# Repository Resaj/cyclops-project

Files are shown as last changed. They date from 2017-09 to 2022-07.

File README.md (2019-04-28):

# Cyclops-project

Robot siguelíneas Open Source, diseñado para introducir a nuevos constructores en la robótica de competición. Se compone de dos PCBs: la del chasis autosoportado con la electrónica principal; y la de sensores, que es intercambiable para poder adaptarlo a diferentes pruebas de seguimiento de línea. Incorpora extras de sensores de distancia, cámara y bluetooth, para poder participar en otras pruebas como carreras y laberinto, además de experimentar nuevos métodos de seguimiento de línea o degradado.

El chasis del robot incorpora:
- Arduino nano
- Batería Lipo 2S
- Pulsadores de selección de menú
- Leds indicadores
- Driver de motores TB6612FNG
- Micromotores 10:1 HP 6V con reductora metálica y encoders en cuadratura
- Ruedas de 32mm de diámetro
- Sensor frontal de distancia de 80cm para detección de oponentes (necesario para carreras)
- Sensores laterales de distancia de 35cm para detección de oponentes (necesario para carreras)
- Cámara de 1x128 píxeles para seguimiento de línea y detección de oponentes
- Expansor I2C para poder soportar todos los periféricos incorporados

La PCB de sensores es intercambiable e incorpora:
- Sensores CNY70 para seguimiento de línea (6 para velocista; 8 para rastreador)
- Multiplexor para los sensores de línea

<p align="center">
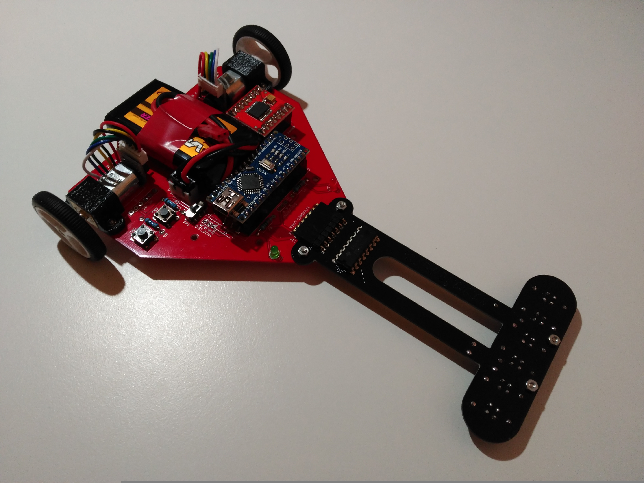
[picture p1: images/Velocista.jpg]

</p>

<p align="center">
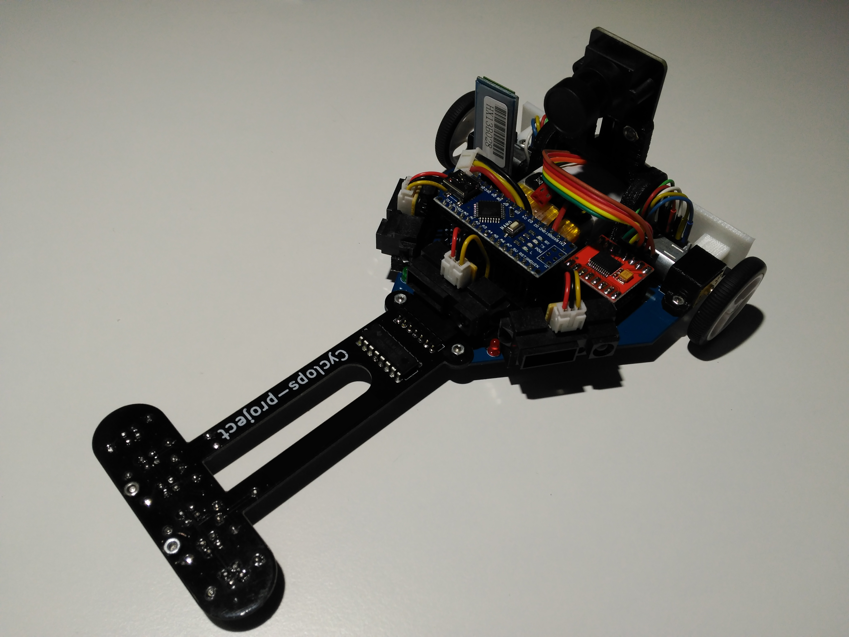
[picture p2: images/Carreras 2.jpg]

</p>

<p align="center">
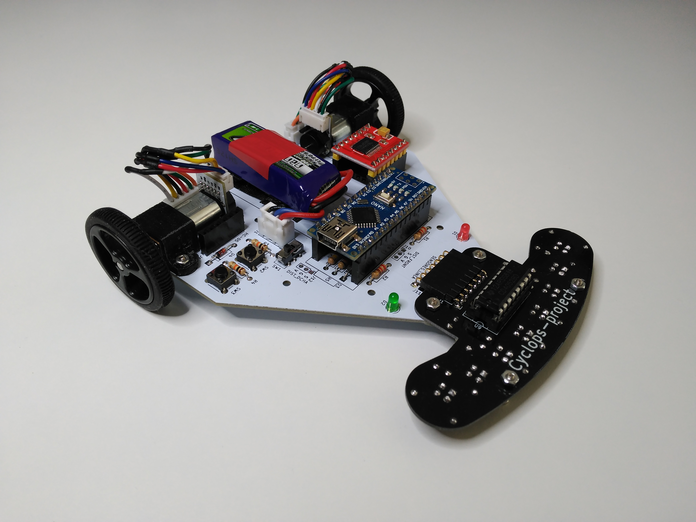
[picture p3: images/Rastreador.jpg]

</p>

## Manuales y guías del proyecto

Disponibles en la carpeta [manuals](https://github.com/Resaj/cyclops-project/tree/master/manuals):
- [Tutorial 1](https://github.com/Resaj/cyclops-project/blob/master/manuals/Tutorial%201%20-%20Bater%C3%ADas%20Lipo.pdf) - Baterías Lipo
- [Tutorial 2](https://github.com/Resaj/cyclops-project/blob/master/manuals/Tutorial%202%20-%20Impresi%C3%B3n%20de%20las%20piezas%20del%20robot.pdf) - Impresión de las piezas del robot
- [Tutorial 3](https://github.com/Resaj/cyclops-project/blob/master/manuals/Tutorial%203%20-%20Montaje%20del%20robot.pdf) - Montaje del robot
- [Tutorial 4](https://github.com/Resaj/cyclops-project/blob/master/manuals/Tutorial%204%20-%20Configuraci%C3%B3n%20del%20bluetooth%20HC-05.pdf) - Configuración del Bluetooth HC-05
- [Tutorial 5](https://github.com/Resaj/cyclops-project/blob/master/manuals/Tutorial%205%20-%20Primeras%20pruebas.pdf) - Primeras pruebas

A medida que el proyecto vaya avanzando se añadirán más tutoriales para completar la información y facilitar el montaje y la programación del robot.

## Retos planteados para el usuario

Cyclops es un proyecto base para cualquier persona que quiera adentrarse en el mundo de la robótica a través de las competiciones. Por un lado se proporciona una base para el aprendizaje y para facilitar la participación; por otro, se plantean una serie de retos e ideas que servirán a los usuarios para afrontar el desarrollo de un proyecto de robótica y profundizar experimentando con las mejoras:

* General:
  * Mejoras de comunicación por bluetooth con logs de telemetría
*  Rastreador:
  * [Reconocimiento de marcas de giro y selección del camino correcto en las bifurcaciones](https://www.youtube.com/watch?v=3Fi3WpjZuA0)
* Velocistas:
  * Reconocimiento de la [pista](https://github.com/Resaj/basic-circuit-maker) con encoders para acelerar en las rectas y frenar antes de las curvas
  * Adaptación del PID de seguimiento de línea para competir sobre [pistas de degradado](https://github.com/Resaj/circuit-maker)
* Carreras:
  * Detección de oponentes con los sensores de distancia para cambiar de carril y efectuar adelantamientos
  * Implementación de un PID para seguir a un oponente en carreras cuando no se pueda cambiar de carril para adelantar
  * Reconocimiento y seguimiento de líneas y degradados con cámara
* Laberinto:
  * Adaptación del algoritmo de laberinto para seguir la pared derecha en vez de la izquierda
  * Guiarse con los dos sensores laterales y con los encoders para ir siempre centrado en las casillas del laberinto
  * Memorizar las casillas del laberinto en el primer intento para que el robot sea capaz de resolverlo al segundo intento tomando el camino más corto

## Preguntas frecuentes

Puedes encontrar un listado de las preguntas frecuentes con sus respectivas respuestas en la [wiki del proyecto](https://github.com/Resaj/cyclops-project/wiki/FAQ).

## Autor

[Rubén Espino San José](https://github.com/Resaj)

## Agradecimientos y aportaciones

- A Alex @TCRobotics de BricoLabs, por su [tutorial para adaptar el driver CH340G de la Arduino Nano para MAC OS](https://bricolabs.cc/wiki/guias/mac_os_y_ch340)
- A [José Luis Villarejo](https://github.com/movilujo), por los [diseños de las PCBs de Cyclops en FreeCAD](https://github.com/Resaj/cyclops-project/tree/master/hw/FreeCAD/PCBs)
- A [Juan Alberto Babío](https://github.com/jbabio), por la adaptación del [soporte regulable para la cámara](https://github.com/Resaj/cyclops-project/blob/master/hw/FreeCAD/Soporte_inclinable_camara_Aliexpress.stl)
- A Óscar de BricoGeek, por sus streaming ([1](https://www.youtube.com/watch?v=NNreAwnH6MY) y [2](https://www.youtube.com/watch?v=S61M1Ss7pH4)) del montaje de Cyclops-Project
- A [Álex](https://github.com/robotaleh) y [Manuel](https://github.com/20leunam), de [OPRobots](https://github.com/OPRobots), por su [App para calibrar y controlar el robot mediante el bluetooth del móvil](https://github.com/Resaj/cyclops-project/tree/master/fw/PID_seguimiento_linea/PID_seguimiento_linea_PIDfromBT)
- A [Javier Martín](https://github.com/jamarju), por su [adaptación del bootloader de la Arduino para la carga de programas por bluetooth](https://github.com/jamarju/hexloader-avr)

## Licencia

<p align="center">



</p>

Todos estos productos están liberados mediante [Creative Commons Attribution-ShareAlike 4.0 International License](http://creativecommons.org/licenses/by-sa/4.0/).

_All these products are released under [Creative Commons Attribution-ShareAlike 4.0 International License](http://creativecommons.org/licenses/by-sa/4.0/)._

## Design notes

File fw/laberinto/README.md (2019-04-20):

# Programa de laberinto

Este programa sirve para testear el funcionamiento de un algoritmo PID básico para entrar y salir de un laberinto. Se trata de seguir una de las dos paredes. Por defecto está programado para que siga la pared izquierda.

Para que todo funcione correctamente debes haber seguido las indicaciones del [tutorial de primeras pruebas](https://github.com/Resaj/cyclops-project/blob/master/manuals/Tutorial%205%20-%20Primeras%20pruebas.pdf), donde aparecen las configuraciones necesarias para las diferentes partes del robot.

El led verde parpadeando indica que se encuentra en el estado "PARADO", preparado para correr. Para ponerlo en marcha hay que pulsar el botón izquierdo; para pararlo, el derecho.

El led rojo indica que la batería está baja.

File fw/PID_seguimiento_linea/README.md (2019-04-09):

# Programa PID_seguimiento_linea

Este programa sirve para testear el funcionamiento de un algoritmo PID básico para el seguimiento de líneas con el robot.

Para que todo funcione correctamente debes haber seguido las indicaciones del [tutorial de primeras pruebas](https://github.com/Resaj/cyclops-project/blob/master/manuals/Tutorial%205%20-%20Primeras%20pruebas.pdf), donde aparecen las configuraciones necesarias para las diferentes partes del robot.

Por defecto, el programa sigue la línea con los sensores de optorreflectancia, pero puede seguirla con la cámara si se descomenta la siguiente línea al comienzo del programa:

``` #define SEGUIMIENTO_CON_CAMARA ```

Para controlarlo se emplea la siguiente máquina de estados:

<p align="center">
<img src="maquina_de_estados.png" width="500" align = "center">
</p>

y los siguientes caracteres, que se envían como comandos a través de bluetooth o USB:
- '0' -> Parar (muy útil para parada de emergencia cuando se escapa el robot)
- '-' -> Bajar velocidad
- '+' -> Subir velocidad
- '1' -> Bajar Kp
- '7' -> Subir Kp
- '2' -> Bajar Ki
- '8' -> Subir Ki
- '3' -> Bajar Kd
- '9' -> Subir Kd

El led rojo indica que la batería está baja.

El led verde puede indicar lo siguiente:
- Si es fijo, se encuentra en el estado "INICIALIZADO".
- Si se enciende y se queda fijo mientras se encuentra en el estado "CALIBRANDO_SENSORES", quiere decir que los umbrales son aceptables y hay margen para una lectura correcta de la línea.
- Si parpadea, se encuentra en el estado "PARADO", preparado para correr.

Hay que tener en cuenta que, en el estado "CALIBRANDO_SENSORES", hay que mover el robot sobre la línea para que los sensores tomen los valores mínimos y máximos para poder calcular un umbral adecuado entre blanco y negro. Pulsar entonces el pulsador derecho para pasar al estado "PARADO". Es posible que al calibrar la cámara en este punto no se encienda el led verde porque los umbrales de blanco y negro son muy próximos entre ellos. El potenciómetro trasero de la cámara ajusta la ganancia de salida, modificando los valores de blanco y negro, pero aún así es difícil conseguir un buen resultado.

# Programa PID_seguimiento_linea_PIDfromBT

Una variante de PID_seguimiento_linea es el programa que puede encontrarse en la carpeta "PID_seguimiento_linea_PIDfromBT", adaptado por OPRobots para controlar el robot mediante su App para móvil, [PIDfromBT](https://github.com/robotaleh/PIDfromBT). La funcionalidad es la misma, pero el control puede realizarse desde el móvil.

Antes de cargarlo hay que instalar previamente su librería [PIDfromBTlib](https://github.com/robotaleh/PIDfromBTlib).

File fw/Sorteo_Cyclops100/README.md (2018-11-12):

# PROGRAMA PARA SORTEAR EL KIT 100 DE CYCLOPS-PROJECT EN LA OSHWDEM 2018

Este programa sirve para realizar un sorteo mediante la generación de un número aleatorio en el rango de números especificados. Para ello basta con fijar el número de participantes en el sorteo, cargar el programa en la Arduino de un Cyclops y abrir Monitor Serial, Putty o cualquier otro terminal que pueda comunicarse con el puerto serie de la Arduino. También se puede especificar el nombre de cada participante. Tras activar el pulsador aparecerá el número resultante en la pantalla.

El número obtenido es el resto de la división del número de milisegundos transcurridos desde el encendido de la Arduino (utilizando la función 'millis') entre el número de participantes.
Al utilizar la función 'millis' es imposible determinar de antemano cuál será el resultado del sorteo.
Por ejemplo:
- Hay 15 participantes
- El pulsador se ha activado en el milisegundo 5621
- El resto de 5621/15 es 11
- El afortunado es el participante con el número 11

Ya que el número 0 no se suele asignar a ningún participante en el sorteo, si saliese el 0 como el resto de la división mencionada anteriormente, el afortunado sería el participante con el número correspondiente al del número de participantes.
Por ejemplo:
- Hay 15 participantes
- El pulsador se ha activado en el milisegundo 9345
- El resto de 9345/15 es 0
- El afortunado es el participante número 15
Por eso en el código aparece el índice 0 asignado al participante con el número más alto.

-----------------------------------------------------

Finalmente, los ganadores del kit #100 de Cyclops-Project en la OSHWDem 2018 fueron los constructores de Pinturillo. ¡¡Enhorabuena!! :-)

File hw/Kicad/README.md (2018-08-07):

Las huellas de componentes empleadas en el diseño e incluídas en las subcarpetas .pretty pertenecen al repositorio [kicad-footprints](https://github.com/KiCad/kicad-footprints).
Igualmente, los ficheros 3D empleados en el diseño e incluidos en las subcarpetas .3dshapes pertenecen al repositorio [kicad-packages3D](https://github.com/KiCad/kicad-packages3D).

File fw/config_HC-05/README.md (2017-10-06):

Este programa se emplea para crear un puente mediante una Arduino entre el ordenador y el bluetooth HC-05 del robot para configurarlo. Utiliza el puerto serie para comunicarse con el ordenador; mientras que para la comunicación con el bluetooth se emplea la librería "SoftSerial" con los pines 9 y 10 de la Arduino.

Puede encontrarse más información en el "Manual de configuración del bluetooth", dentro de la carpeta "manuals".

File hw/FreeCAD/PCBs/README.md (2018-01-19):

# Diseño FreeCad de las PCB de Cyclops

El diseño de las placas se ha realizado partiendo del diseño en KiCad y usando el banco de trabajo de FreeCAD - [Printed Circuit Board](https://sourceforge.net/projects/eaglepcb2freecad/), tal y como se cuenta en este [tutorial](http://diwo.bq.com/creando-los-modelos-3d-de-nuestros-circuitos-con-freecad/).

Algunos de los componentes no existían en la base original de la herramienta, por lo que se han importado del repositorio de [FreeCad](https://github.com/FreeCAD/FreeCAD-library).

<p align="center">
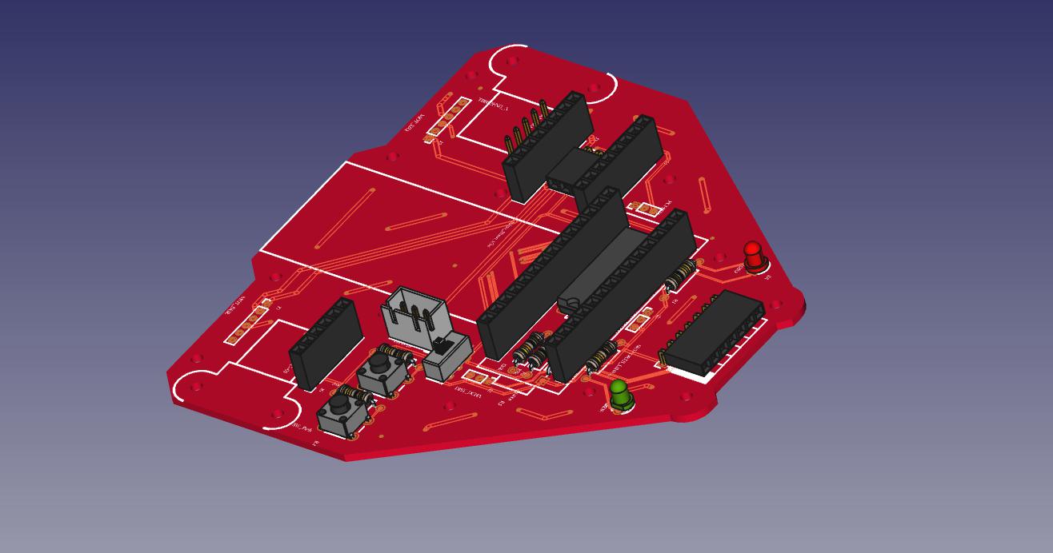
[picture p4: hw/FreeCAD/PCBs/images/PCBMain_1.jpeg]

</p>

<p align="center">
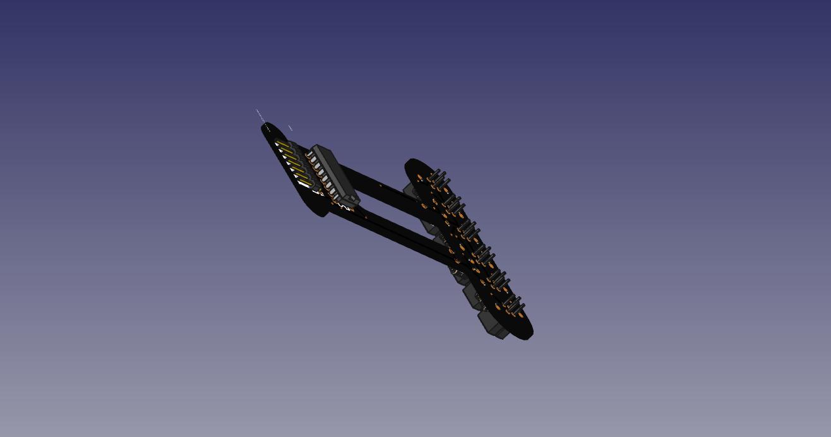
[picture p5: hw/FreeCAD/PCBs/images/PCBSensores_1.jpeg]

</p>

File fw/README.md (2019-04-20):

Para realizar las primeras pruebas de programación se recomienda seguir el [tutorial 5](https://github.com/Resaj/cyclops-project/blob/master/manuals/Tutorial%205%20-%20Primeras%20pruebas.pdf), disponible en la carpeta "manuals", en el cual se describen las librerías necesarias para que los programas compilen correctamente y las configuraciones para el funcionamiento adecuado del robot.

Para facilitar la instalación de las librerías, éstas se incluyen en la carpeta "libraries".

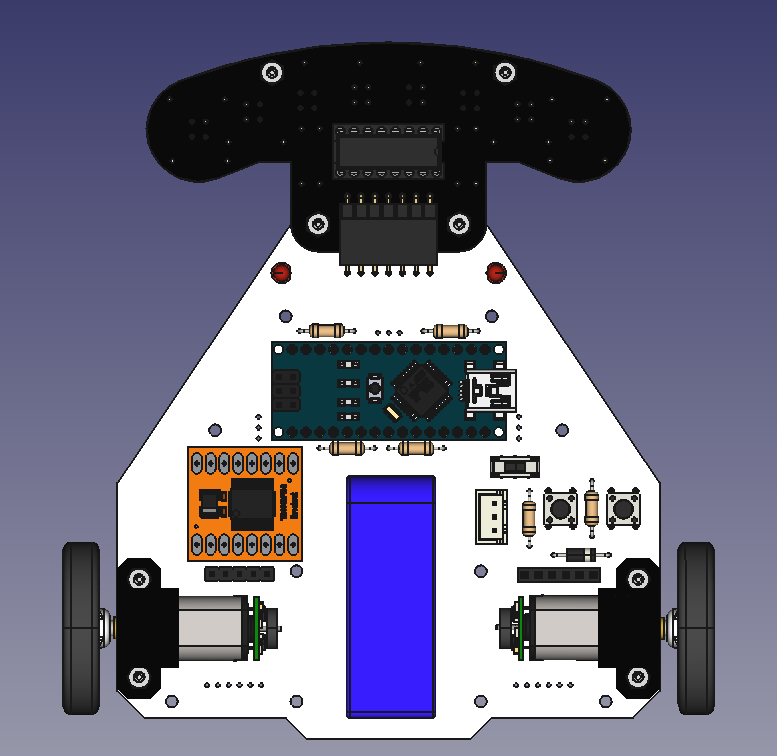
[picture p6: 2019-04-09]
images/3D/Rastreador top.png

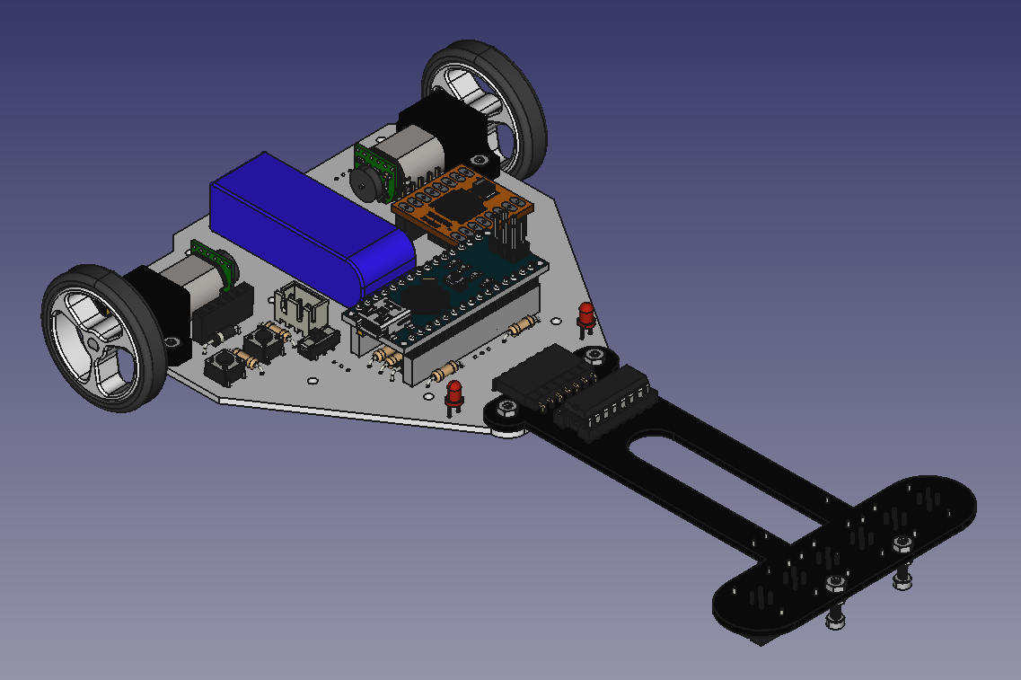
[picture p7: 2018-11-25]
images/3D/Velocista.png

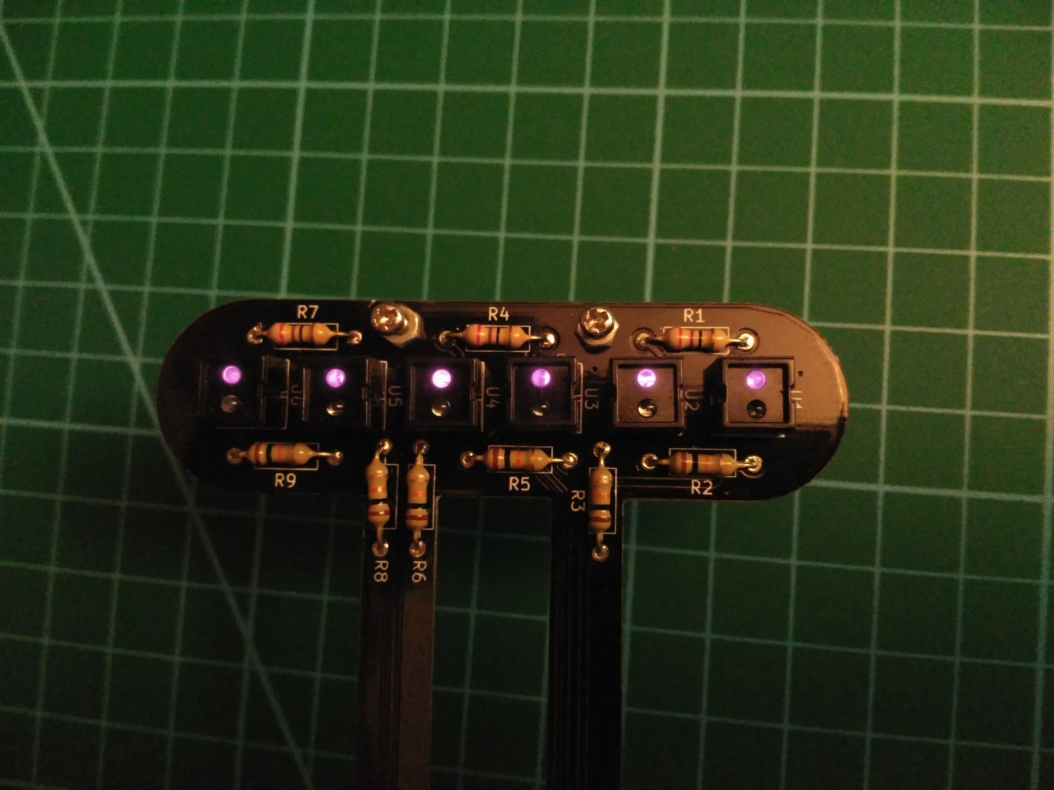
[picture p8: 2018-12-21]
images/Wiki/Luz CNY70.jpg

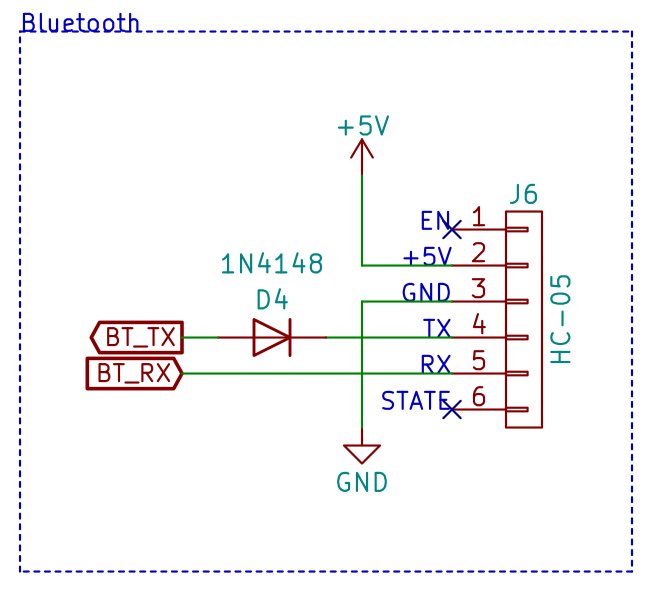
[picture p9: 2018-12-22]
images/Wiki/Esquema bluetooth.png

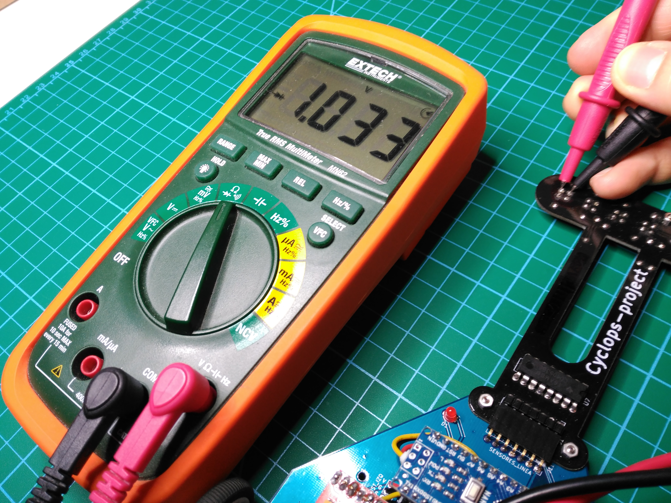
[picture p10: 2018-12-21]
images/Wiki/Comprobar CNY70 (1).jpg

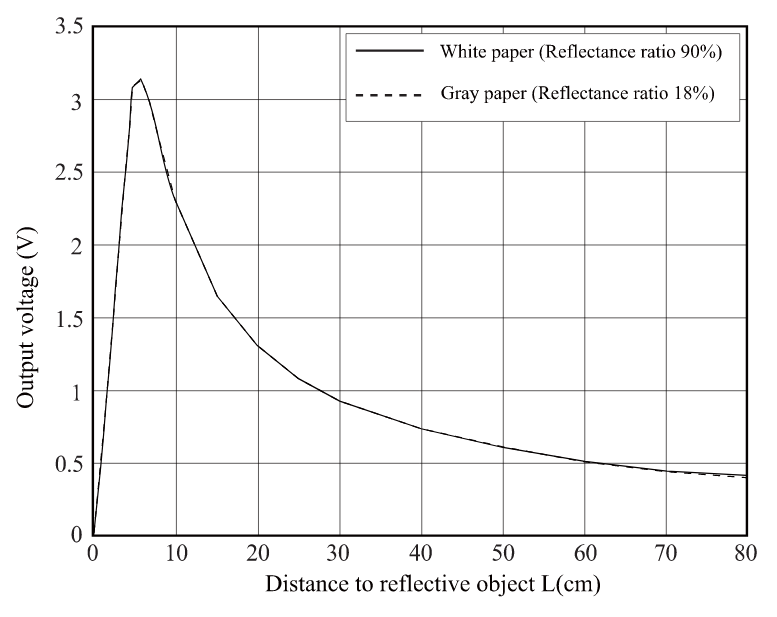
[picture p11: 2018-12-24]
images/Wiki/GP2Y0A21 function.png

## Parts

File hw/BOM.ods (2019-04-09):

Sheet: BOM
Artículo | Unidades | Coste/Unidad (€) | Coste total (€) | Enlace
CHASIS
Placa principal | 1 | 4,55 | 4,55 | PCBway (https://www.pcbway.com/pcb_prototype/)
Batería | 1 | 2,86 | 2,86 | eBay (http://www.ebay.com/itm/291988892787)
Velcro adhesivo | 1 | 1,00 | 1,00
Micro motor con encoder, cableado y con conector 2 mm 6 pines | 2 | 11,10 | 22,19 | Alibaba (https://www.alibaba.com/product-detail/GM12-gear-motor-w-encoder-3_60638952365.html)
Conector 2mm 6 pines para el motor | 2 | 0,14 | 0,28 | Aliexpress (https://es.aliexpress.com/store/product/50pcs-male-material-PH2-0-Connectors-Leads-pin-Header-PH-A/2260001_32744043213.html)
Par de ruedas | 1 | 4,30 | 4,30 | TME (http://www.tme.eu/es/details/pololu-1088/micromotores-y-accesorios/pololu/pololu-wheel-32x7mm-pair-_-white/)
Soporte de motores impreso en 3D | 2
Tornillo M2x5mm para motores e interconexión de placas | 6 | 0,03 | 0,17 | Aliexpress (https://es.aliexpress.com/store/product/50Pcs-lot-Screw-M2-5-of-Screws-Nuts-Assortment-Bolts-Screw-Spike-Round-Head-Screw-2mm/804316_32722845879.html)
Tuerca M2 para motores e interconexión de placas | 6 | 0,01 | 0,06 | Aliexpress (https://es.aliexpress.com/store/product/m2-500pcs-low-price-nut-china-fasteners-hexagon-head-nuts-Manufacturer/1504033_32258654248.html)
Conector batería | 1 | 0,08 | 0,08 | eBay (http://www.ebay.com/itm/10pcs-RC-2S-7-4V-Lipo-Battery-Balance-Charger-JST-XH-Connector-Plug-White-/182523055031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)
Interruptor | 1 | 0,05 | 0,05 | Aliexpress (https://es.aliexpress.com/item/C18-New-Hot-50Pcs-Slide-Switch-6-Pin-Mini-Toggle-Switch-SMD-PCB-2-Position-DPDT/32656635939.html)
Conversor DC-DC | 1 | 1,21 | 1,21 | Aliexpress (https://es.aliexpress.com/item/Adjustable-Step-Down-Module-Mini-DC-DC-12-24V-To-5V-3A-Buck-Converter-Efficiency-97/32725685606.html)
Arduino nano | 1 | 2,13 | 2,13 | Aliexpress (https://es.aliexpress.com/item/1PCS-Nano-3-0-controller-compatible-with-nano-CH340-USB-driver-NO-CABLE-for-Arduino-NANO/32706132765.html)
Driver de motores | 1 | 1,49 | 1,49 | Aliexpress (https://es.aliexpress.com/item/1pcs-lot-Dual-Motor-Driver-1A-TB6612FNG-forArduino-Microcontroller-Better-than-L298N/32789439915.html)
Tira de conectores macho | 1 | 0,10 | 0,10 | Aliexpress (https://es.aliexpress.com/store/product/10pcs-40-Pin-1x40-Single-Row-Male-2-54-Breakable-Pin-Header-Connector-Strip-for-Arduino/1948124_32641752713.html)
Tira de conectores macho extendida | 1 | 0,22 | 0,22 | Aliexpress (https://es.aliexpress.com/store/product/20pcs-lot-2-54mm-1-40pin-single-row-straight-Needle-total-high-25MM-Connector-Pin-Header/1952980_32654605158.html)
Tira de conectores hembra | 2 | 0,18 | 0,36 | Aliexpress (https://es.aliexpress.com/store/product/Free-Shipping-10PCS-40pin-2-54mm-pitch-single-row-11mm-row-female-connectors/221555_1929060681.html)
Tira de conectores macho acodados | 1 | 0,32 | 0,32 | Aliexpress (https://es.aliexpress.com/store/product/10PC-Lot-2X40P-2-54MM-10-5mm-Height-Dual-Row-Male-Pin-Header-Connector-Free-Shipping/513417_32647668402.html)
Tira de conectores hembra acodados | 1 | 0,23 | 0,23 | Aliexpress (https://es.aliexpress.com/store/product/10pcs-1x40-Pin-2-54mm-Right-Angle-Single-Row-Female-Pin-Header-Connector/1769158_32326267382.html)
Resistencia 220 Ohm 1/4W | 2 | 0,01 | 0,02 | eBay (http://www.ebay.com/itm/100PCS-1-4W-Watt-220-ohm-220R-Metal-Film-Resistor-0-25W-1-RoHS-/291634347420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)
Resistencia 1k 1/4W | 2 | 0,01 | 0,02 | eBay (http://www.ebay.com/itm/100PCS-1-4W-Watt-1k-ohm-1k-Metal-Film-Resistor-0-25W-1-RoHS-/291634550250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)
Resistencia 10k 1/4W | 2 | 0,01 | 0,02 | eBay (http://www.ebay.com/itm/100pcs-1-4w-Watt-10K-ohm-10Kohm-Metal-Film-Resistor-0-25W-100000R-1-/381374783687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)
Resistencia 82k 1/4W | 1 | 0,01 | 0,01 | eBay (http://www.ebay.com/itm/100PCS-1-4W-Watt-82K-ohm-Metal-Film-Resistor-0-25W-1-RoHS-/291634574265)
Resistencia 120k 1/4W | 1 | 0,01 | 0,01 | eBay (http://www.ebay.com/itm/100PCS-1-4W-Watt-120K-ohm-Metal-Film-Resistor-0-25W-1-RoHS-/291634574846)
Diodo 1N4001 | 1 | 0,01 | 0,01 | eBay (http://www.ebay.com/itm/100x-Silicon-Rectifier-1A-Diode-1N4001-1N4002-1N4003-1N4004-1N4005-1N4006-DO-41-/401361485516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)
Expansor I2C PCF8574AP | 1 | 0,84 | 0,84 | eBay (http://www.ebay.com/itm/292143242967?_trksid=p2060353.m2749.l2649&ssPageName=STRK%3AMEBIDX%3AIT)
Zócalo DIP 16 pines | 1 | 0,08 | 0,08 | TME (https://www.tme.eu/en/details/icvt-16p/standard-dip-sockets/connfly/ds1009-16at1nx/)
Led rojo 3mm | 1 | 0,01 | 0,01 | eBay (http://www.ebay.com/itm/N-100pcs-Lot-3mm-White-Green-Red-Blue-Yellow-LED-Light-Bulb-Emitting-Diode-Lamps-/332247927770)
Led verde 3mm | 1 | 0,01 | 0,01 | eBay (http://www.ebay.com/itm/100PCS-Diffused-LED-3MM-GREEN-COLOR-GREEN-LIGHT-Super-Bright-CA-NEW-/141976472523)
Pulsador | 2 | 0,02 | 0,04 | Aliexpress (https://es.aliexpress.com/item/50pcs-lot-6x6x4-3MM-4PIN-G89-Tactile-Tact-Push-Button-Micro-Switch-Direct-Plug-in-Self/32669948621.html)
Cable USB a miniUSB | 1 | 0,79 | 0,79 | eBay (http://www.ebay.com/itm/Black-2-0-USB-Cable-Type-A-to-Mini-B-Male-To-Male-5-PIN-Charger-Cable-For-Phone-/272361596849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)
MORRO DE SENSORES DE VELOCISTA Y CARRERAS
Placa de sensores de velocista | 1 | 4,55 | 4,55 | PCBway (https://www.pcbway.com/pcb_prototype/)
Tornillo M2x8mm para apoyos | 2 | 0,01 | 0,02 | Aliexpress (https://es.aliexpress.com/store/product/100PCS-Stainless-Steel-M2-x-8mm-Screw-Cross-Round-Head-Philips-Head-Screws-Hex-Socket-Button/120565_32716321685.html)
Tuerca M2 para apoyos | 4 | 0,01 | 0,04 | Aliexpress (https://es.aliexpress.com/store/product/m2-500pcs-low-price-nut-china-fasteners-hexagon-head-nuts-Manufacturer/1504033_32258654248.html)
Sensores de línea CNY70 | 6 | 0,24 | 1,44 | eBay (http://www.ebay.com/itm/10PCS-CNY70-Reflective-Optical-Sensor-with-Transistor-output-Vishay-NEW-/171540640561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)
Resistencia 82 Ohm 1/4W (o 27 Ohmios para CNY70 piratas) | 3 | 0,01 | 0,03 | eBay (http://www.ebay.com/itm/100-pcs-1-4W-0-25W-1-Metal-Film-Resistor-82-ohm-82ohm/282035611771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) | eBay (http://www.ebay.com/itm/100pcs-1-4W-Watt-0-25W-Metal-Film-Resistor-27ohm-1-precision-/291872266166)
Resistencia 10k 1/4W | 6 | 0,01 | 0,05 | eBay (http://www.ebay.com/itm/100pcs-1-4w-Watt-10K-ohm-10Kohm-Metal-Film-Resistor-0-25W-100000R-1-/381374783687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)
Zócalo DIP 16 pines | 1 | 0,08 | 0,08 | TME (https://www.tme.eu/en/details/icvt-16p/standard-dip-sockets/connfly/ds1009-16at1nx/)
Multiplexor CD4053BE | 1 | 0,10 | 0,10 | Aliexpress (https://es.aliexpress.com/store/product/FREE-SHIPPING-10PCS-CD4053BE-CD4053-DIP-16-Analog-Multiplexer-IC/1762665_32724299198.html)
MORRO DE SENSORES DE RASTREADOR
Placa de sensores de rastreador | 1 | 4,55 | 4,55 | PCBway (https://www.pcbway.com/pcb_prototype/)
Tornillo M2x8mm para apoyos | 2 | 0,01 | 0,02 | Aliexpress (https://es.aliexpress.com/store/product/100PCS-Stainless-Steel-M2-x-8mm-Screw-Cross-Round-Head-Philips-Head-Screws-Hex-Socket-Button/120565_32716321685.html)
Tuerca M2 para apoyos | 4 | 0,01 | 0,04 | Aliexpress (https://es.aliexpress.com/store/product/m2-500pcs-low-price-nut-china-fasteners-hexagon-head-nuts-Manufacturer/1504033_32258654248.html)
Resistencia 82 Ohm 1/4W (o 27 Ohmios para CNY70 piratas) | 4 | 0,01 | 0,03 | eBay (http://www.ebay.com/itm/100-pcs-1-4W-0-25W-1-Metal-Film-Resistor-82-ohm-82ohm/282035611771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) | eBay (http://www.ebay.com/itm/100pcs-1-4W-Watt-0-25W-Metal-Film-Resistor-27ohm-1-precision-/291872266166)
Resistencia 10k 1/4W | 6 | 0,01 | 0,05 | eBay (http://www.ebay.com/itm/100pcs-1-4w-Watt-10K-ohm-10Kohm-Metal-Film-Resistor-0-25W-100000R-1-/381374783687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)
Sensores de línea CNY70 | 6 | 0,24 | 1,44 | eBay (http://www.ebay.com/itm/10PCS-CNY70-Reflective-Optical-Sensor-with-Transistor-output-Vishay-NEW-/171540640561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)
Zócalo DIP 16 pines | 1 | 0,08 | 0,08 | TME (https://www.tme.eu/en/details/icvt-16p/standard-dip-sockets/connfly/ds1009-16at1nx/)
Multiplexor CD4052BE | 1 | 0,35 | 0,35 | TME (https://www.tme.eu/es/details/cd4052be/descodificadores-multiplexores-interru/texas-instruments/)
EXTRAS PARA CARRERAS
Sensor de distancia frontal GP2Y0A21 | 1 | 2,98 | 2,98 | eBay (http://www.ebay.com/itm/1PCS-Sharp-GP2Y0A21YK0F-GP2Y0A21-10-80cm-Infrared-Proximity-Distance-Sensor-M70-/301724765196)
Sensores de distancia laterales GP2Y0A41 | 2 | 3,77 | 7,54 | eBay (http://www.ebay.com/itm/Sharp-GP2Y0A41SK0F-Infrared-Proximity-Sensor-Range-4-30cm-cabl-GP2D120-M67-/291550089372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)
Soporte de sensores de distancia impreso en 3D | 1
Pantalla trasera impresa en 3D | 1
Tornillo M2x5mm para soporte de sensores y pantalla | 6 | 0,03 | 0,17 | Aliexpress (https://es.aliexpress.com/store/product/50Pcs-lot-Screw-M2-5-of-Screws-Nuts-Assortment-Bolts-Screw-Spike-Round-Head-Screw-2mm/804316_32722845879.html)
Tuerca M2 para soporte de sensores y pantalla | 6 | 0,01 | 0,06 | Aliexpress (https://es.aliexpress.com/store/product/m2-500pcs-low-price-nut-china-fasteners-hexagon-head-nuts-Manufacturer/1504033_32258654248.html)
EXTRA COMUNICACIÓN INALÁMBRICA
Bluetooth HC-05 con placa de conexión | 1 | 2,85 | 2,85 | eBay (http://www.ebay.com/itm/1-5-10PCS-HC-06-HC-05-30ft-Wireless-Bluetooth-RF-Transceiver-Module-RS232-TTL-/282221351296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)
Diodo 1N4148 | 1 | 0,01 | 0,01 | Aliexpress (https://es.aliexpress.com/store/product/Free-shipping-100PCS-do-35-1N4148-IN4148-High-speed-switching-diodes/1496311_32825954883.html) | Únicamente para la segunda versión de la PCB principal
EXTRA CÁMARA
Cámara TSL1401 | 1 | 12,66 | 12,66 | Aliexpress (https://es.aliexpress.com/store/product/Linear-CCD-line-array-module-TSL1401-camera-module-with-wide-range-of-adjustable-output-signal/2274002_32695140018.html)
Tornillo M3x6mm para cámara | 2 | 0,02 | 0,04 | Aliexpress (https://es.aliexpress.com/store/product/50pcs-M3-x6mm-Steel-Head-Screws-Bolts-Nuts-Hex-Socket-Head-Cap-Screw-Bolts-Self-Tapping/120565_32717104392.html)
Tuerca M3 para cámara | 2 | 0,01 | 0,02 | Aliexpress (https://es.aliexpress.com/store/product/100pcs-lot-M3-Screw-Nut-Hex-Nuts-Hexagonal-3mm-For-Coupler-Motor-Mount-Servo-Bracket-Robot/2781221_32796257468.html)
Tornillo M2x5mm para soporte de cámara | 4 | 0,03 | 0,11 | Aliexpress (https://es.aliexpress.com/store/product/50Pcs-lot-Screw-M2-5-of-Screws-Nuts-Assortment-Bolts-Screw-Spike-Round-Head-Screw-2mm/804316_32722845879.html)
Tuerca M2 para soporte de cámara | 4 | 0,01 | 0,04 | Aliexpress (https://es.aliexpress.com/store/product/m2-500pcs-low-price-nut-china-fasteners-hexagon-head-nuts-Manufacturer/1504033_32258654248.html)
5x Cable hembra-hembra 10cm | 1 | 0,12 | 0,12 | Aliexpress (https://es.aliexpress.com/store/product/40pcs-lot-10cm-2-54mm-1pin-Female-to-Female-jumper-wire-Dupont-cable/1326062_32566719482.html)
Soporte de cámara impreso en 3D | 1
EXTRAS NECESARIOS
Cargador lipo 2S | 1 | 6,15 | 6,15 | Aliexpress (https://es.aliexpress.com/item/F08474-IMAX-RC-B3-Pro-Compact-Balance-Charger-for-2S-3S-7-4V-11-1V-Lithium/32240245610.html)
 |  | Subtotal (€) | 89,04 |  |  | Conversión €/$
 |  | Gastos de envío PCBway (€) | 11,82 |  |  | 0,85348
 |  | Gastos de envío TME (€) | 9,56
 |  | Total (€) | 110,41

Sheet: Lista_de_componentes
Artículo | Unidades
CHASIS
Placa principal | 1
Batería | 1
Velcro adhesivo | 1
Micro motor con encoder, cableado y con conector 2mm 6 pines | 2
Conector 2mm 6 pines para el motor | 2
Par de ruedas | 1
Soporte de motores impreso en 3D | 2
Tornillo M2x5mm para motores e interconexión de placas | 6
Tuerca M2 para motores e interconexión de placas | 6
Conector batería lipo 2S | 1
Interruptor | 1
Conversor DC-DC | 1
Arduino nano con conectores macho verticales | 1
Driver de motores con conectores macho verticales | 1
Conector hembra vertical 15 pines para Arduino nano | 2
Conector hembra vertical 8 pines para driver de motores | 2
Conector hembra acodado 4 pines para conversor DC-DC | 1
Conector macho acodado 4 pines para conversor DC-DC | 1
Conector hembra acodado 7 pines para interconexión de placas | 1
Resistencia 220 Ohm 1/4W | 2
Resistencia 1k 1/4W | 2
Resistencia 10k 1/4W | 2
Resistencia 82k 1/4W | 1
Resistencia 120k 1/4W | 1
Diodo 1N4001 | 1
Expansor I2C PCF8574AP | 1
Zócalo DIP 16 pines | 1
Led rojo 3mm | 1
Led verde 3mm | 1
Pulsador | 2
Cable USB a miniUSB | 1
MORRO DE SENSORES DE VELOCISTA Y CARRERAS
Placa de sensores | 1
Tornillo M2x10mm para apoyos | 2
Tuerca M2 para apoyos | 4
Sensor CNY70 | 6
Conector macho acodado 7 pines para interconexión de placas | 1
Resistencia 82 o 27 Ohm 1/4W | 3
Resistencia 10k 1/4W | 6
Zócalo DIP 16 pines | 1
Multiplexor CD4053BE | 1
MORRO DE SENSORES DE RASTREADOR
Placa de sensores | 1
Tornillo M2x10mm para apoyos | 2
Tuerca M2 para apoyos | 4
Sensor CNY70 | 8
Conector macho acodado 7 pines para interconexión de placas | 1
Resistencia 82 o 27 Ohm 1/4W | 4
Resistencia 10k 1/4W | 8
Zócalo DIP 16 pines | 1
Multiplexor CD4052BE | 1
EXTRAS PARA CARRERAS
Sensor de distancia frontal GP2Y0A21 con cable | 1
Sensor de distancia lateral GP2Y0A41 con cable | 2
Conector macho vertical extendido 15 pines para Arduino nano | 2
Soporte de sensores de distancia impreso en 3D | 1
Pantalla trasera impresa en 3D | 1
Tornillo M2x5mm para soporte de sensores y pantalla | 6
Tuerca M2 para soporte de sensores y pantalla | 6
EXTRA COMUNICACIÓN INALÁMBRICA
Bluetooth HC-05 con placa de conexión | 1
Diodo 1N4148 | 1 | Únicamente para la segunda versión de la PCB principal
Conector hembra vertical 6 pines | 1
EXTRA CÁMARA
Cámara TSL1401 | 1
Conector macho vertical 5 pines | 1
Tornillo M3x6mm para cámara | 2
Tuerca M3 para cámara | 2
Tornillo M2x5mm para soporte de cámara | 4
Tuerca M2 para soporte de cámara | 4
Bus de 5 cables hembra-hembra 10cm | 1
Soporte de cámara impreso en 3D | 1

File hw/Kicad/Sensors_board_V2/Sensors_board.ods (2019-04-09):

Reference | Value | Footprint | Datasheet
R1 | 82 | Resistors_THT:R_Axial_DIN0207_L6.3mm_D2.5mm_P10.16mm_Horizontal
R4 | 82 | Resistors_THT:R_Axial_DIN0207_L6.3mm_D2.5mm_P10.16mm_Horizontal
R7 | 82 | Resistors_THT:R_Axial_DIN0207_L6.3mm_D2.5mm_P10.16mm_Horizontal
R10 | 82 | Resistors_THT:R_Axial_DIN0207_L6.3mm_D2.5mm_P10.16mm_Horizontal
R2 | 10k | Resistors_THT:R_Axial_DIN0207_L6.3mm_D2.5mm_P10.16mm_Horizontal
R3 | 10k | Resistors_THT:R_Axial_DIN0207_L6.3mm_D2.5mm_P10.16mm_Horizontal
R5 | 10k | Resistors_THT:R_Axial_DIN0207_L6.3mm_D2.5mm_P10.16mm_Horizontal
R6 | 10k | Resistors_THT:R_Axial_DIN0207_L6.3mm_D2.5mm_P10.16mm_Horizontal
R8 | 10k | Resistors_THT:R_Axial_DIN0207_L6.3mm_D2.5mm_P10.16mm_Horizontal
R9 | 10k | Resistors_THT:R_Axial_DIN0207_L6.3mm_D2.5mm_P10.16mm_Horizontal
R11 | 10k | Resistors_THT:R_Axial_DIN0207_L6.3mm_D2.5mm_P10.16mm_Horizontal
R12 | 10k | Resistors_THT:R_Axial_DIN0207_L6.3mm_D2.5mm_P10.16mm_Horizontal
J1 | SENSORES_LINEA | Pin_Headers:Pin_Header_Angled_1x07_Pitch2.54mm
U9 | 4052 | Housings_DIP:DIP-16_W7.62mm_LongPads
U1 | CNY70 | Sensors_board:CNY70
U2 | CNY70 | Sensors_board:CNY70
U3 | CNY70 | Sensors_board:CNY70
U4 | CNY70 | Sensors_board:CNY70
U5 | CNY70 | Sensors_board:CNY70
U6 | CNY70 | Sensors_board:CNY70
U7 | CNY70 | Sensors_board:CNY70
U8 | CNY70 | Sensors_board:CNY70

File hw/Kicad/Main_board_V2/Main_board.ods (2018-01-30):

Reference | Value | Footprint | Datasheet
J1 | LIPO 2S | Connectors_JST:JST_XH_B03B-XH-A_03x2.50mm_Straight
J8 | DIST_IZQ | Socket_Strips:Socket_Strip_Straight_1x03_Pitch2.00mm
J10 | DIST_FRONT | Socket_Strips:Socket_Strip_Straight_1x03_Pitch2.00mm
J12 | DIST_DCHA | Socket_Strips:Socket_Strip_Straight_1x03_Pitch2.00mm
R1 | 220 | Resistors_THT:R_Axial_DIN0207_L6.3mm_D2.5mm_P10.16mm_Horizontal
R2 | 220 | Resistors_THT:R_Axial_DIN0207_L6.3mm_D2.5mm_P10.16mm_Horizontal
J6 | HC-05 | Socket_Strips:Socket_Strip_Straight_1x06_Pitch2.54mm
D1 | ROJO | LEDs:LED_D3.0mm
D2 | VERDE | LEDs:LED_D3.0mm
R5 | 82k | Resistors_THT:R_Axial_DIN0207_L6.3mm_D2.5mm_P10.16mm_Horizontal
R6 | 120k | Resistors_THT:R_Axial_DIN0207_L6.3mm_D2.5mm_P10.16mm_Horizontal
D3 | 1N4001 | Diodes_THT:D_A-405_P10.16mm_Horizontal
D4 | 1N4148 | Diodes_THT:D_A-405_P10.16mm_Horizontal
SW2 | SW_Push | Buttons_Switches_THT:SW_PUSH_6mm
SW3 | SW_Push | Buttons_Switches_THT:SW_PUSH_6mm
R3 | 10K | Resistors_THT:R_Axial_DIN0207_L6.3mm_D2.5mm_P10.16mm_Horizontal
R4 | 10K | Resistors_THT:R_Axial_DIN0207_L6.3mm_D2.5mm_P10.16mm_Horizontal
J2 | MOT_IZQ | Socket_Strips:Socket_Strip_Straight_1x06_Pitch2.00mm
J7 | MOT_DER | Socket_Strips:Socket_Strip_Straight_1x06_Pitch2.00mm
J9 | CAMARA | Socket_Strips:Socket_Strip_Straight_1x05_Pitch2.54mm
J5 | DC-DC_5V | Socket_Strips:Socket_Strip_Angled_1x04_Pitch2.54mm
A1 | Arduino_Nano_v3.x | Modules:Arduino_Nano
JP1 | Jumper | Connectors:GS2
J3 | TB6612FNG_A | Socket_Strips:Socket_Strip_Straight_1x08_Pitch2.54mm
J4 | TB6612FNG_B | Socket_Strips:Socket_Strip_Straight_1x08_Pitch2.54mm
J11 | SENSORES_LINEA | Socket_Strips:Socket_Strip_Angled_1x07_Pitch2.54mm
U1 | PCF8574 | Housings_DIP:DIP-16_W7.62mm_LongPads
SW1 | SW_DPDT | Main_board:switch_DPDT
R7 | 1K | Resistors_THT:R_Axial_DIN0207_L6.3mm_D2.5mm_P10.16mm_Horizontal
R8 | 1K | Resistors_THT:R_Axial_DIN0207_L6.3mm_D2.5mm_P10.16mm_Horizontal

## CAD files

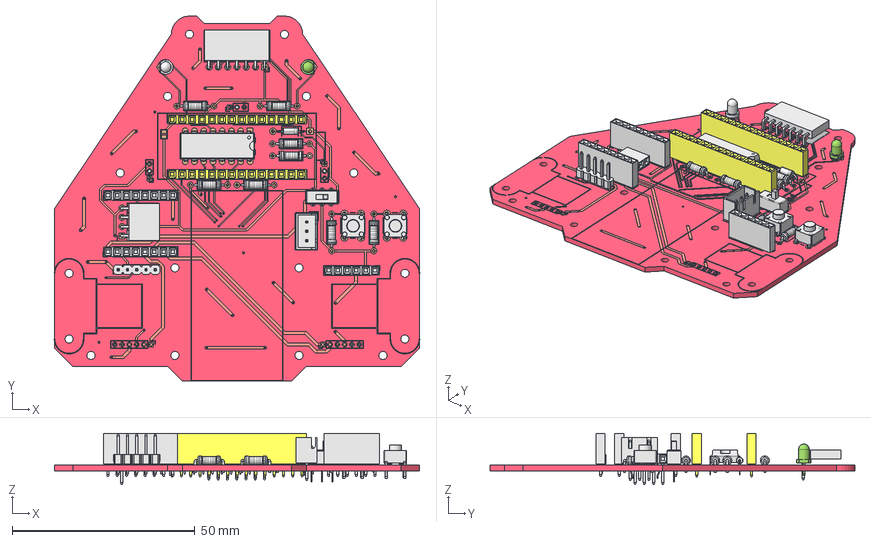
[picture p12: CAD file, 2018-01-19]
hw/FreeCAD/PCBs/cyclops_mainPCB.FCStd
100.2 x 100.0 x 14.0 mm
Board
R1
R2
R3
R4
R5
R6
R7
R8
D1
D2
SW2
SW3
U1
J3
J4
J6
J9
J5
J11
D3
SW1
J1
F_Cu_0
bPad_107
tPad_108
B_Cu_31
F_SilkS_37
csFemale-pin-header
csFemale-pin-header001

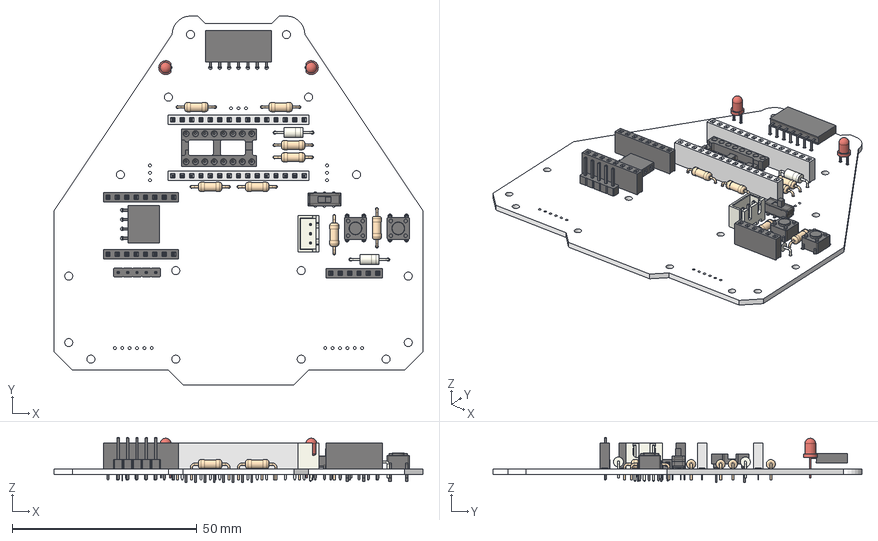
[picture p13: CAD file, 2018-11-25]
hw/Kicad/Main_board_V2/Main_board_V2.FCStd
100.0 x 100.0 x 12.3 mm
Pcb
Arduino_Nano_
LED_D3.0mm_
LED_D3.0mm_001
JST_B03B_XH_A_
PinSocket_1x08_P254mm_Vertical_
PinSocket_1x08_P254mm_Vertical_001
PinSocket_1x04_P254mm_Horizontal_
PinSocket_1x06_P254mm_Vertical_
PinHeader_1x05_P254mm_Vertical_
PinSocket_1x07_P254mm_Horizontal_
R_Axial_DIN0207_L63mm_D25mm_P1016mm_Horizontal_
R_Axial_DIN0207_L63mm_D25mm_P1016mm_Horizontal_001
R_Axial_DIN0207_L63mm_D25mm_P1016mm_Horizontal_002
R_Axial_DIN0207_L63mm_D25mm_P1016mm_Horizontal_003
R_Axial_DIN0207_L63mm_D25mm_P1016mm_Horizontal_004
R_Axial_DIN0207_L63mm_D25mm_P1016mm_Horizontal_005
R_Axial_DIN0207_L63mm_D25mm_P1016mm_Horizontal_006
R_Axial_DIN0207_L63mm_D25mm_P1016mm_Horizontal_007
CuK_JS202011CQN_DPDT_straight_
SW_PUSH_6mm_
SW_PUSH_6mm_001
DIP_16_W762mm_Socket_
D_A-405_P10.16mm_Horizontal_
D_A-405_P10.16mm_Horizontal_001

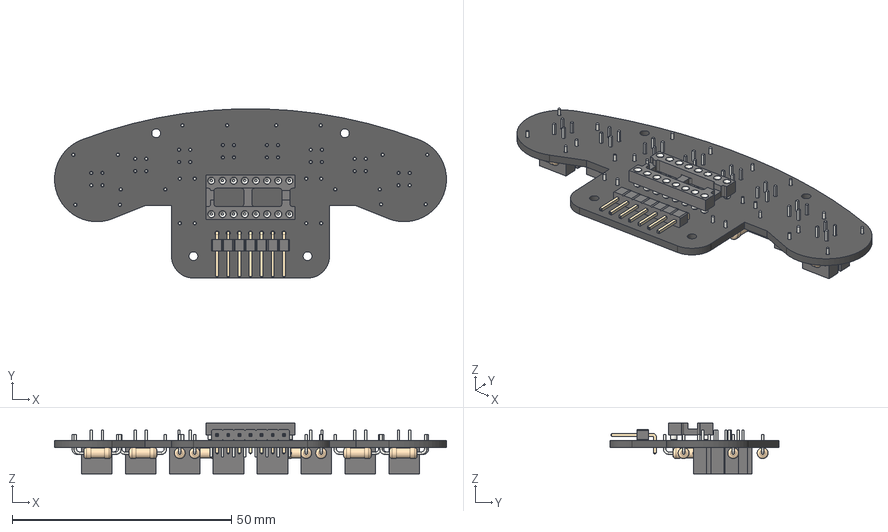
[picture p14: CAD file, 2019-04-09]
hw/FreeCAD/Ensamble Cyclops/Sensors_board_V2.step
89.3 x 38.5 x 11.6 mm
Pcb
PCB_Sketch
PinHeader_1x07_P254mm_Horizontal_
DIP_16_W762mm_Socket_
Vishay_CNY70_
Vishay_CNY70_001
R_Axial_DIN0207_L63mm_D25mm_P1016mm_Horizontal_
Vishay_CNY70_002
Vishay_CNY70_003
R_Axial_DIN0207_L63mm_D25mm_P1016mm_Horizontal_001
Vishay_CNY70_004
Vishay_CNY70_005
R_Axial_DIN0207_L63mm_D25mm_P1016mm_Horizontal_002
R_Axial_DIN0207_L63mm_D25mm_P1016mm_Horizontal_003
R_Axial_DIN0207_L63mm_D25mm_P1016mm_Horizontal_004
R_Axial_DIN0207_L63mm_D25mm_P1016mm_Horizontal_005
R_Axial_DIN0207_L63mm_D25mm_P1016mm_Horizontal_006
R_Axial_DIN0207_L63mm_D25mm_P1016mm_Horizontal_007
R_Axial_DIN0207_L63mm_D25mm_P1016mm_Horizontal_008
R_Axial_DIN0207_L63mm_D25mm_P1016mm_Horizontal_009
R_Axial_DIN0207_L63mm_D25mm_P1016mm_Horizontal_010
R_Axial_DIN0207_L63mm_D25mm_P1016mm_Horizontal_011
Vishay_CNY70_006
Vishay_CNY70_007

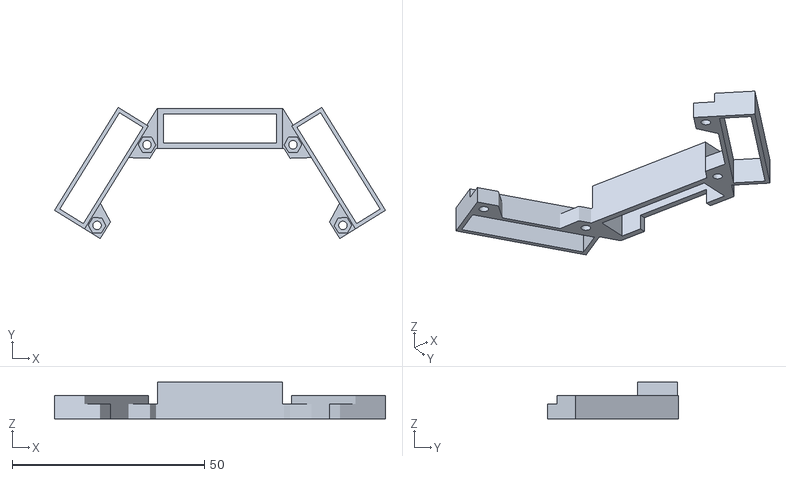
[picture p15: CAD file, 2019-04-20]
hw/FreeCAD/Soporte sensores de distancia.stl
86.2 x 34.2 x 9.55

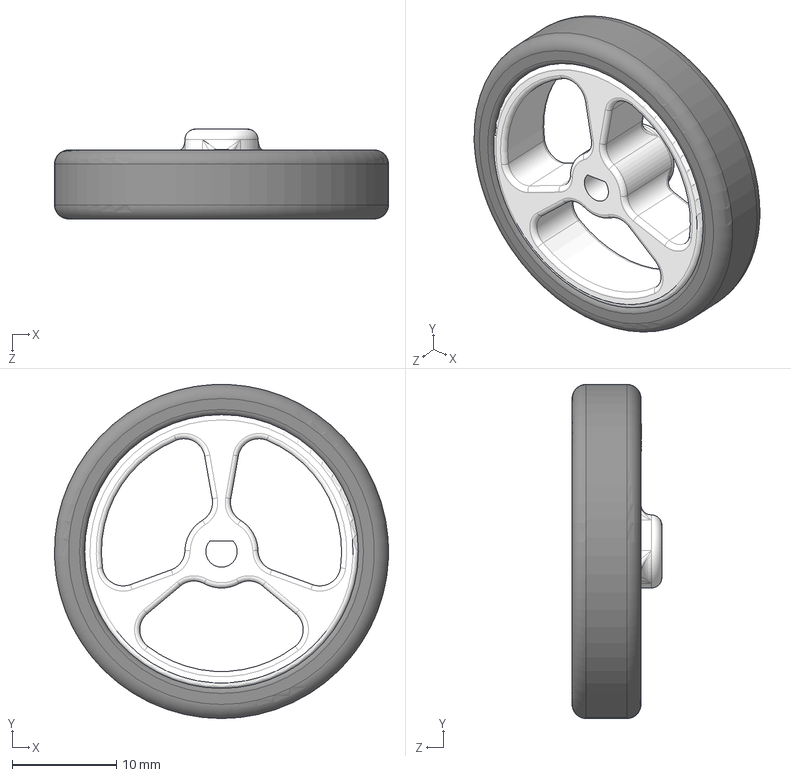
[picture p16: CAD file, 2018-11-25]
hw/FreeCAD/Ensamble Cyclops/Wheel.step
32.0 x 32.0 x 8.60 mm

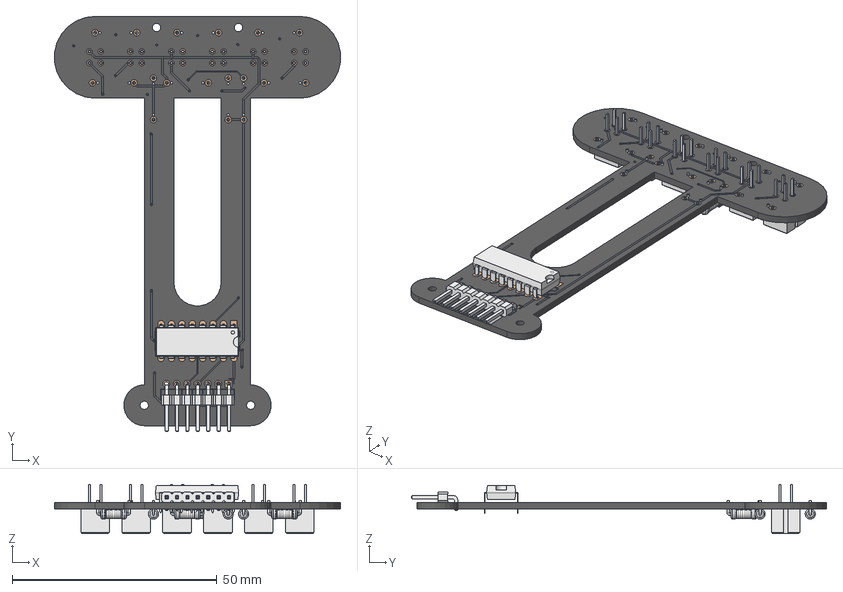
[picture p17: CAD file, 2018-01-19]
hw/FreeCAD/PCBs/cyclops_sensorPCB.FCStd
69.9 x 101.4 x 12.0 mm
Board
R1
R2
R3
R4
R5
R6
R7
R8
R9
J1
U7
U6
U5
U4
U3
U2
U1
F_Cu_0
bPad_107
tPad_108
B_Cu_31
B_SilkS_36
F_SilkS_37

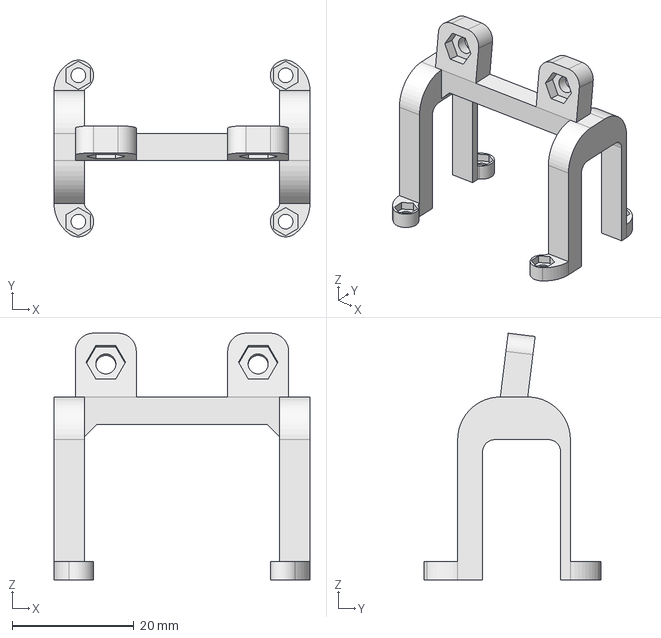
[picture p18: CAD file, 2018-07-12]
hw/FreeCAD/Soporte camara APTech.FCStd
42.0 x 29.0 x 40.5 mm

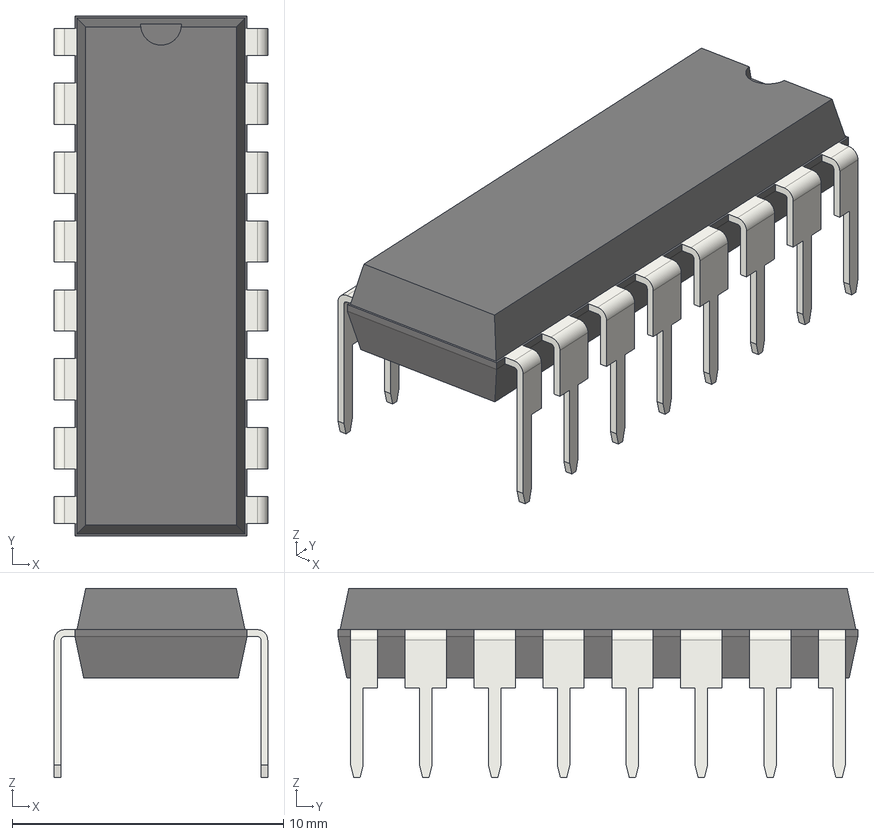
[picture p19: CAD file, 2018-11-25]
hw/FreeCAD/Ensamble Cyclops/DIP-16_W7.62mm.step
7.87 x 19.2 x 6.98 mm

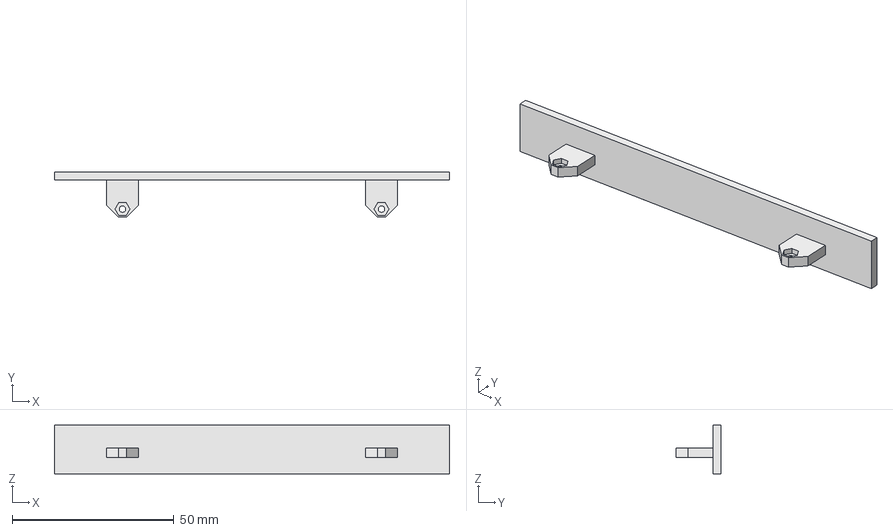
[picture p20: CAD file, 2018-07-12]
hw/FreeCAD/Pantalla trasera.FCStd
122.0 x 14.0 x 15.0 mm

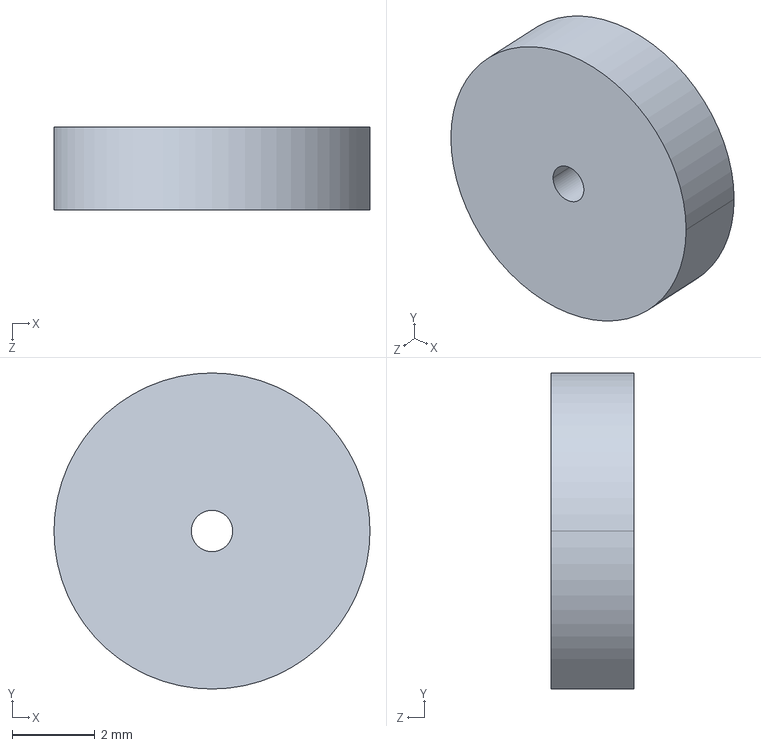
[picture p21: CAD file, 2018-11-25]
hw/FreeCAD/Ensamble Cyclops/Encoder disc.step
7.65 x 7.65 x 2.00 mm

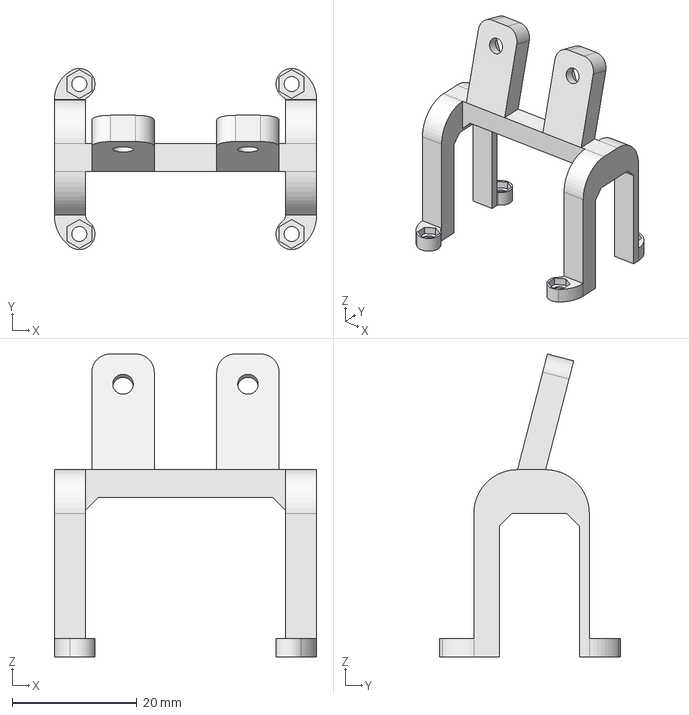
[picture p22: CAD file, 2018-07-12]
hw/FreeCAD/Soporte camara Aliexpress.FCStd
42.0 x 29.0 x 48.5 mm

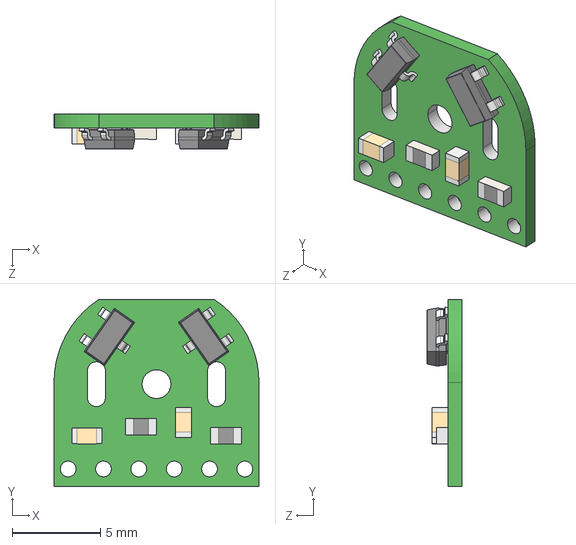
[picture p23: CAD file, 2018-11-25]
hw/FreeCAD/Ensamble Cyclops/Magnetic encoder.step
11.6 x 10.6 x 1.99 mm

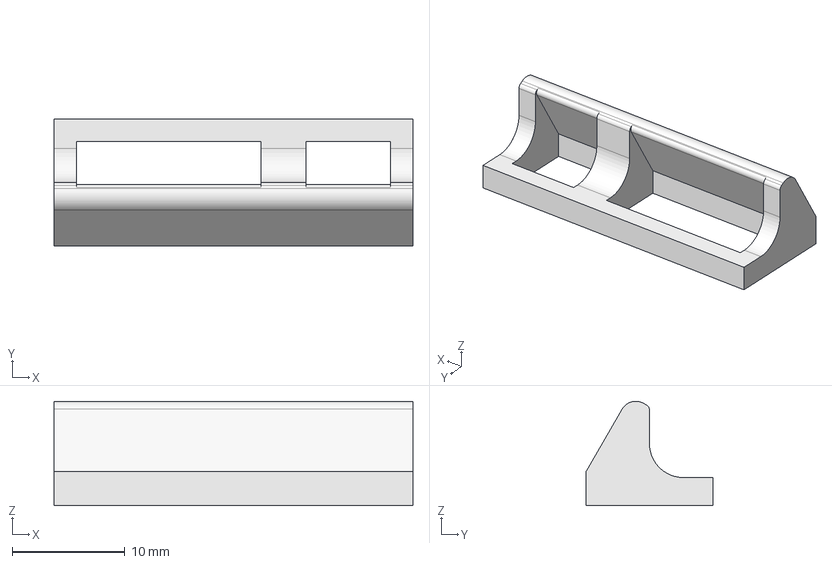
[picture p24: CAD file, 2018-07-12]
hw/FreeCAD/Visera sensor de distancia.FCStd
31.9 x 11.2 x 9.27 mm

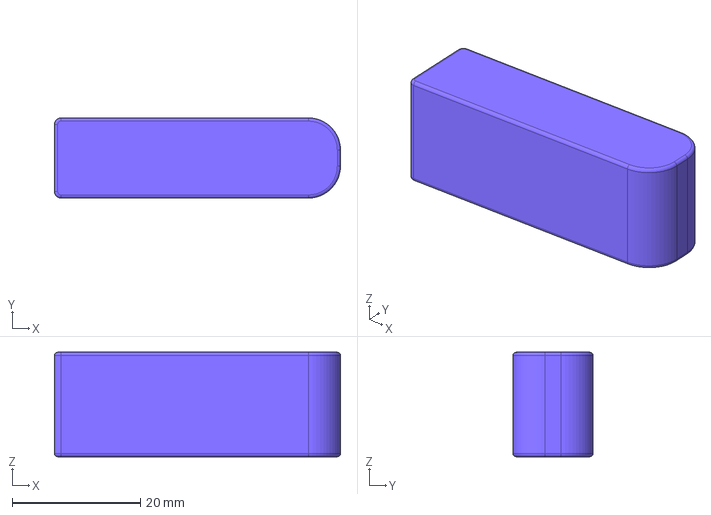
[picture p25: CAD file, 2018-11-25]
hw/FreeCAD/Ensamble Cyclops/Lipo battery 2S.step
44.6 x 12.5 x 16.3 mm

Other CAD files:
hw/FreeCAD/Soporte de sensores de distancia.FCStd
hw/FreeCAD/Soporte_inclinable_camara_Aliexpress.stl
hw/FreeCAD/Soporte micromotor (tornillos M2).stl
hw/FreeCAD/Ensamble Cyclops/Lipo battery 2S.fcstd
hw/FreeCAD/Ensamble Cyclops/M2 nut.STEP
hw/FreeCAD/Ensamble Cyclops/M2x10 screw.STEP
hw/FreeCAD/Ensamble Cyclops/M2x5 screw.STEP
hw/FreeCAD/Ensamble Cyclops/Sensors_board.step
hw/FreeCAD/Pantalla trasera.stl
hw/FreeCAD/Soporte camara APTech.stl
hw/FreeCAD/Soporte camara Aliexpress.stl
hw/FreeCAD/Visera sensor de distancia.stl
hw/Kicad/Sensors_board/Sensors_board.FCStd
hw/Kicad/Sensors_board/Sensors_board.step
hw/Kicad/Sensors_board_V2/Sensors_board_V2.FCStd

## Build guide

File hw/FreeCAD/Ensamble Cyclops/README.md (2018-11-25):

En esta carpeta puede encontrarse el modelo 3D del kit básico de Cyclops-Project para guiarse en su montaje, junto con los diferentes elementos que lo componen.

Algunos de los modelos 3D incluidos en el diseño han sido descargados de webs de terceros:
- Librerías de Kicad: [componentes electrónicos](https://github.com/KiCad)
- Pololu: [Micro motor](https://www.pololu.com/product/2211/resources), [Wheel](https://www.pololu.com/product/1088/resources), [Magnetic encoder y Encoder disc](https://www.pololu.com/product/3081)
- GrabCAD: [Arduino Nano](https://grabcad.com/library/arduino-nano--1) y [Driver de motores](https://grabcad.com/library/sparkfun-motor-driver-dual-tb6612fng-1a-1), [M2 nut, M2x5 screw y M2x10 screw](https://grabcad.com/library/all-m2-sh-standard-screws-m2-hex-nut-and-flat-washer-for-m2-screw-1)

El uso de la herramienta [Kicad Step Up](https://sourceforge.net/projects/kicadstepup/) en FreeCAD permite importar directamente el archivo kicadpcb del proyecto de Kicad para generar los modelos 3D de las PCBs con sus componentes, sincronizados con las librerías de Kicad mencionadas más arriba.

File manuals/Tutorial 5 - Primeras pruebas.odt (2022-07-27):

Primeras pruebas de programación

Antes de comenzar, ¿tu ordenador es Mac? En ese caso puede que experimentes algunos problemas con el driver CH340G de la Arduino Nano, por lo que te sugiero que sigas este tutorial para adaptar el CH340G a MAC OS, de Alex @TCRobotics de BricoLabs (https://bricolabs.cc/wiki/guias/mac_os_y_ch340).

Librerías

La única librería imprescindible para que el robot funcione es la librería SoftWire. Es necesaria para comunicarse por bus I2C al expansor I2C, ya que debido a la cantidad de entradas/salidas necesarias no se ha podido implementar en el bus I2C que Arduino trae por defecto, sino en dos pines digitales cualquiera. Precisamente por la gran cantidad de entradas/salidas necesarias ha sido por lo que se ha decidido incluir un expansor I2C para poder conectar más dispositivos.

Para facilitar la instalación de las librerías, éstas se incluyen comprimidas en la carpeta fw/libraries dentro del repositorio.

Si prefieres descargar la librería SoftWire directamente de la web, puedes encontrarla en el siguiente enlace: https://github.com/felias-fogg/SoftI2CMaster

Las librerías que necesites deberás descomprimirlas y copiarlas a tu carpeta de Arduino/libraries. Si no la tienes localizada, abre el menú Archivo/Preferencias del IDE de Arduino y encontrarás la ruta de tu carpeta de Arduino:

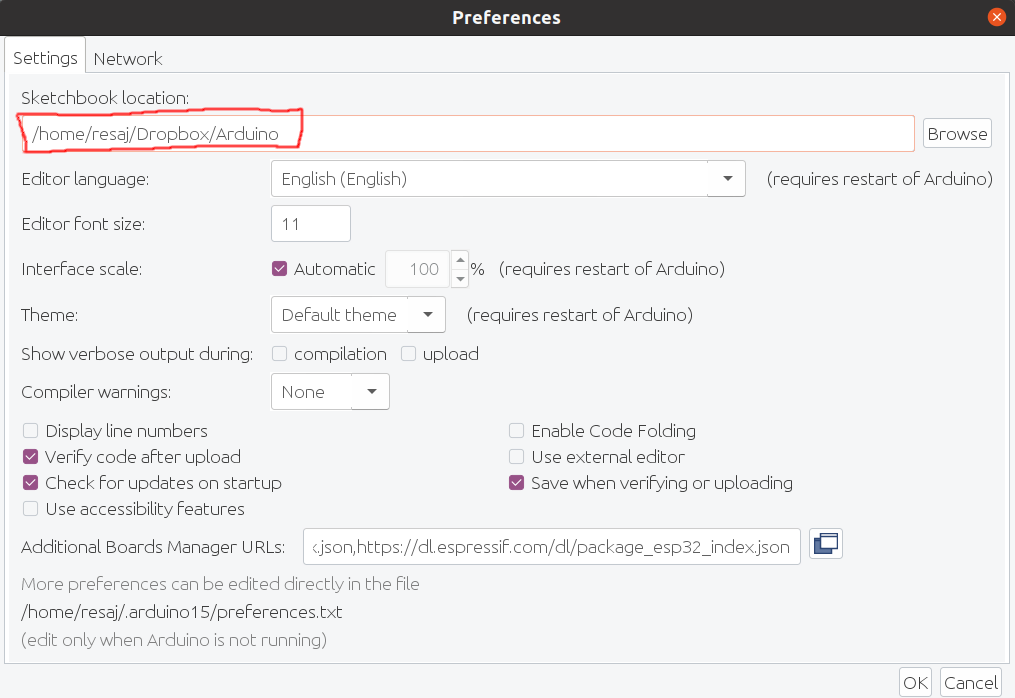
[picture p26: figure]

Consideraciones para la programación

Debido a la existencia de algunas diferencias entre los kits de Cyclops-project, cabe mencionarlas para evitar conflictos con la programación:

- Por la falta de pines de entrada/salida disponibles, el Bluetooth comparte puerto serie con el USB de programación de la Arduino, por lo que con la primera versión de la PCB principal es necesario desconectar el Bluetooth para poder cargar los programas en la Arduino. De hecho, el Bluetooth está pensado para hacer pruebas en movimiento, corriendo sobre algún circuito, para enviar telemetría y recibir órdenes sin el cable USB.

Si la PCB principal lleva por detrás la inscripción “Main_board_V2”, se tratará de la segunda versión, en la cual se ha solucionado ese problema añadiendo un diodo en el diseño. En este caso no hará falta desconectar el Bluetooth para la carga de programas.

- Se aconseja que el baudrate declarado para el puerto serie sea siempre el mismo y que coincida con el que se ha programado en el Bluetooth siguiendo su tutorial de configuración. Así se podrá cambiar de USB a Bluetooth y viceversa sin necesidad de cambiar el baudrate.
- Para seleccionar la placa de sensores de línea del robot hay que comentar/descomentar la siguiente línea de código:

#define SENSORES_LINEA_VELOCISTA

Si se deja descomentada, se utilizará la placa de sensores para velocistas (V1); pero si se comenta, el código pondrá por defecto la opción de placa de sensores para rastreador (V2).

- Existen dos tipos de expansor I2C que sirven y se han empleado en Cyclops-Project hasta ahora: PCF8574P y PCF8574AP. Funcionan exactamente igual a nivel de hardware, pero para poder comunicarse con ellos, hay que hacer uso de direcciones I2C diferentes:
  - PCF8574P: utiliza la dirección hexadecimal 0x20, teniendo sus tres pines físicos de dirección conectados a masa.
  - PCF8574AP: utiliza la dirección hexadecimal 0x38, teniendo sus tres pines físicos de dirección conectados a masa.

El valor de dirección se puede modificar en la constante expAddress que puede verse declarada en el programa de test. Y para saber cuál es el código de tu expansor, basta con mirar la inscripción en el integrado, que estará justo debajo de la Arduino.

- Sentido de los motores: es probable que los motores se hayan soldado con los pines cambiados, ya que no hay pautas fijas obligatorias para hacerlo. El resultado es que el motor gira al contrario. En este caso lo que habría que hacer es intercambiar, en el programa de test, los valores de los “defines” DIR_IZQ_1 y DIR_IZQ_2, para el motor izquierdo, o DIR_DER_1 y DIR_DER_2, para el motor derecho. Para saber si están girando en el sentido correcto, basta con cargar el programa de test de motores mencionado más adelante y que ambas ruedas comiencen girando de tal manera que el robot avance hacia delante en línea recta.
- Los encoders magnéticos, al igual que los sensores CNY70 o los pulsadores, actúan como transistores o interruptores que abren y cierran un circuito, pero para que a su salida experimenten una variación de tensión de 0 a 5V necesitan una resistencia de pull up. Algunos de los encoders empleados en los kits pueden no llevar esas resistencias. La configuración por defecto en la función de setup es la siguiente:

pinMode(ENC_IZQ_A, INPUT);

pinMode(ENC_IZQ_B, INPUT);

pinMode(ENC_DER_A, INPUT);

pinMode(ENC_DER_B, INPUT);

Pero si no se aprecia variación en Monitor Serial al cargar el programa de test de los encoders y girar las ruedas, es muy probable que sea porque los encoders no tienen resistencias de pull up y aparezcan todos los valores en cero. Bastaría cambiar el código anterior por este otro para utilizar las resistencias internas de la Arduino:

pinMode(ENC_IZQ_A, INPUT_PULLUP);

pinMode(ENC_IZQ_B, INPUT_PULLUP);

pinMode(ENC_DER_A, INPUT_PULLUP);

pinMode(ENC_DER_B, INPUT_PULLUP);

Comprobar que todo funciona correctamente

Se ha diseñado un programa de test para comprobar que todas las partes del robot funcionan correctamente. Este programa se encuentra dentro de la carpeta fw/test del repositorio.

Para probar cada uno de los dispositivos, hay que descomentar la línea correspondiente en la cabecera del programa, cargarlo en la Arduino, y abrir Monitor Serial o Putty con el baudrate que se haya especificado en el firmware, para USB o para Bluetooth:

#define TEST_LEDS

//#define TEST_PULSADORES

//#define TEST_BATERIA

//#define TEST_SENSORES_LINEA

//#define TEST_SENSORES_DISTANCIA

//#define TEST_MOTORES

//#define TEST_ENCODERS

//#define TEST_CAMARA

Se recomienda descomentar únicamente una de las líneas de test cada vez que se vaya a cargar el programa. Así se probará cada parte individualmente para evitar conflictos.

Consideraciones para la carga del programa

Antes de cargar el firmware en tu Cyclops-project tienes que seleccionar algunas opciones en el IDE de Arduino:

- En el menú Herramientas/Placa deberás seleccionar “Arduino Nano”.
- En el menú Herramientas/Procesador selecciona la opción “ATmega328P”, pero si cuando vayas a cargar el programa sale un error, es probable que tengas que seleccionar la opción “ATmega328P (Old Bootloader)”, puesto que algunos Arduino Nano continúan con la versión antigua del bootloader.
- En el menú herramientas/Puerto selecciona el puerto USB al que esté conectado tu Cyclops. Puede ser un COM en Windows o un tty/USB en Ubuntu, por ejemplo.

El entorno y el programa ya estarían listos para poder cargar y probar.

Tutorial de primeras pruebas de programación Rubén Espino San José

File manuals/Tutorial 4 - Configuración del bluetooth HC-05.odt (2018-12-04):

BLUETOOTH HC-05

El módulo HC-05 es un bluetooth muy utilizado en proyectos de electrónica. Es fácilmente programable mediante comandos AT y se conecta por puerto serie.

Antes de trabajar con él requiere ser configurado, para lo cual existen diversos métodos, como el empleo de una Arduino o de un FTDI. Los comandos AT serán introducidos por el Monitor Serial de Arduino o algún otro terminal como Putty. Ya que este proyecto está orientado a programar con Arduino y dispone de una Arduino Nano, se puede utilizar ésta para programar el bluetooth mediante Monitor Serial.

Montaje

Lo primero que hay que hacer es desconectar la Arduino Nano y el bluetooth HC-05 del robot. A continuación, se realiza el siguiente montaje:

- VCC HC-05 -> 5V Arduino Nano
- GND HC-05 -> GND Arduino Nano
- TXD HC-05 -> D10 Arduino Nano
- RXD HC-05 -> D9 Arduino Nano

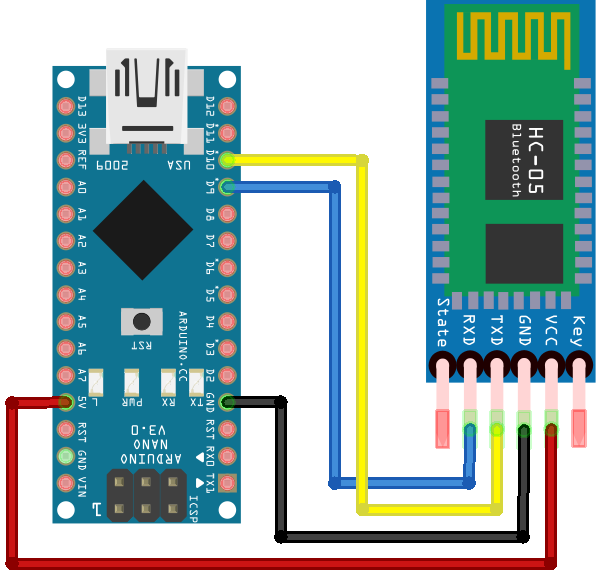
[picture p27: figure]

Programación de la Arduino

Ahora hay que conectar la Arduino por USB al ordenador y cargarle el siguiente programa, que puede encontrarse en la carpeta “fw” del proyecto:

#include <SoftwareSerial.h>

#define TX 9 // RX del HC-05

#define RX 10 // TX del HC-05

SoftwareSerial BTserial(RX, TX);

void setup() {

Serial.begin(9600);

Serial.println("Enviar comandos AT:");

BTserial.begin(38400);

}

void loop() {

if (BTserial.available())

Serial.write(BTserial.read());

if (Serial.available())

BTserial.write(Serial.read());

}

Como puede verse es un programa simple de redireccionamiento de los datos. Todo lo que llega a la Arduino por un puerto, lo reenvía por el otro, a modo de puente entre el ordenador y el bluetooth.

En este punto hay que fijarse en que el baudrate de los puertos serie no es el mismo, aunque podría serlo. Obligatoriamente el del bluetooth ha de ser 38400, ya que es el baudrate que necesita para el modo de configuración del HC-05; mientras que el del puerto serie del ordenador está definido en 9600, que podría cambiarse, siempre y cuando sea el mismo que se especifique en Monitor Serial.

Entrar en modo de configuración

Una vez realizado el montaje y cargado el programa en la Arduino, hay que entrar en el modo de configuración del bluetooth, para ello hay que seguir los siguientes pasos:

1. Desconectar alimentación del bluetooth
2. Pulsar y mantener el botón del bluetooth
3. Conectar alimentación del bluetooth
4. Soltar el pulsador pasados dos segundos

Se apreciará que el parpadeo rápido que antes tenía el led, que indicaba que no estaba conectado a ningún dispositivo, se ha tornado en un parpadeo lento, que indica que está en modo de configuración.

Configuración con los comandos AT

Ahora toca abrir el Monitor Serial de Arduino y seleccionar la transmisión de 9600 baudios y la opción “NL & CR” en el desplegable. Esta última opción es imprescindible, ya que envía el carácter de nueva línea con retorno de carro (más conocido como “intro” o “enter”) tras el mensaje que se envía al pulsar el botón de enviar. Ese intro es necesario, ya que el HC-05 lo interpreta como el final del comando.

Ahora, ¿cuáles son los comandos de configuración del HC-05? Comandos hay muchos, que podréis encontrar en el manual de usuario del bluetooth, pero los que se van a necesitar son los siguientes:

- AT
  - Es el comando más básico y se emplea para ver si hay comunicación con el bluetooth, que debería responder con “OK”.
- AT+NAME=nombre_de_mi_dispositivo
  - Es el comando que da el nombre al dispositivo. Cuando se utiliza, suele sacar al bluetooth del modo de configuración, por lo que hay que volver a entrar en el modo siguiendo el procedimiento del apartado anterior.
- AT+ROLE=0
  - Este comando indica que el bluetooth funciona como esclavo, que es el rol que necesita para poder conectarse al bluetooth del ordenador.
- AT+PSWD=mi_password
  - Con este comando se edita la contraseña del bluetooth, que es la que pedirá el ordenador cuando intente enlazarse.
- AT+UART=38400,0,0
  - Para seleccionar el baudrate se utiliza este comando. El primer número del comando es el baudrate, mientras que los dos ceros que aparecen a continuación son parámetros de configuración de la UART que se suelen dejar en cero. Se puede emplear cualquier baudrate comprendido entre los estándares: 9600, 19200, 38400, 115200… En los programas de ejemplo de la carpeta fw se utiliza 38400 por simplificar, ya que es la velocidad a la que se configura el HC-05, pero si se modifica el baudrate en la programación, será necesario cambiarlo también en la configuración del bluetooth, y viceversa.

Al introducir los comandos anteriores, el bluetooth contesta con OK o con ERROR, indicando si se ha realizado correctamente la operación o si ha habido algún tipo de problema. Pero, ¿cómo saber qué parámetros son los que están configurados sin necesidad de redefinirlos? Basta con utilizar los comandos anteriores seguidos de una interrogación, en vez de un igual con el valor a escribir. Por ejemplo:

- AT+ROLE?
- AT+PSWD?
- AT+UART?

Cada uno de estos comandos hace que el bluetooth devuelva el valor correspondiente por el que se está preguntando. No se incluye el comando “AT+NAME?” porque a veces devuelve un error y no deja ser leído.

Listo para funcionar

El bluetooth ya está configurado. Para salir del modo de configuración basta con desenchufar y volver a enchufar el bluetooth allá donde se quiera utilizar. Este bluetooth ha sido configurado como esclavo, por lo que podría enlazarse con otro HC-05 configurado como máster (en este caso habría que especificar en sus configuraciones las direcciones de los bluetooth mediante otros comandos AT) o con el bluetooth del ordenador (buscando dispositivos bluetooth y agregando nuevo hardware), que es el objetivo principal para poder ver los datos de telemetría que se reciban del robot. Sabremos que están enlazados cuando el led del HC-05 presente un doble parpadeo.

Carga de programas por bluetooth

Por defecto no se puede hacer la carga de los programas por bluetooth en una Arduino, pero este proyecto de Javier Martín (https://github.com/jamarju/hexloader-avr) lo permite.

Este apartado es opcional, pero aconsejable si se tiene un poco de experiencia en electrónica.

Referente al proyecto de carga del programa por el HC-05 se pueden señalar los siguientes puntos:

- La carga se realiza a 115200 baudios, mucho más rápido que a través del IDE de Arduino. Aunque si se desea, se puede modificar con el parámetro BAUD_RATE del fichero /hexloader/hexloader.c.
- El botón de reset conmuta entre la ejecución del programa y el modo de carga (boot).
- El proceso para cargar el programa con el nuevo bootloader es:
  1. Compilar el programa y generar los archivos binarios desde el menú del IDE de Arduino.
  2. Iniciar una sesión enlazando con el bluetooth desde PuTTy (https://www.putty.org/), Cu o cualquier otro terminal que lo permita.
  3. Copiar todo el texto del archivo .hex generado (de los dos generados es el que no lleva el bootloader incluido).
  4. Asegurarse de que la Arduino ha entrado en modo boot. Para ello hay que pulsar reset e instantáneamente el bootloader de la Arduino responderá por pantalla.
  5. Pegar el texto en la sesión abierta. Volver a pegarlo para verificar.
- El fichero de texto .hex se puede recargar cada vez que se genere sin tener que cerrarlo y abrirlo de nuevo.
- Se puede hacer reset por bluetooth llamando a una función (función reset indicada en el Readme del proyecto) cuando se le envíe a la Arduino un determinado comando desde terminal. De esta manera no hace falta ni tocar el robot para programarlo.
- Lo mejor de todo es que la sesión abierta para la comunicación con el bluetooth no hay que cerrarla y volver a abrirla cada vez que se quiera cargar el programa.

Algunos detalles a tener en cuenta si se sigue este punto:

- El HC-05 deberá estar configurado a la misma velocidad que indique el bootloader. Si no se cambia el bootloader, será 115200; pero entonces habrá que modificar el baudrate por defecto de los programas de Cyclops-Project a 115200, en vez de 38400.
- Para cargar el nuevo bootloader en la Arduino Nano habrá que utilizar el programador adecuado de AVR o una Arduino según se indica en el tutorial de ArduinoISP (https://www.arduino.cc/en/Tutorial/ArduinoISP).

Manual de configuración del bluetooth HC-05 Rubén Espino San José

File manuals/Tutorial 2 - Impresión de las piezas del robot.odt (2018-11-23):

Las piezas impresas de Cyclops-Project

En su versión inicial Cyclops-project se compone de hasta 5 piezas impresas:

- Dos soportes de motores (incluidos en el kit básico).
- Un soporte de sensores de distancia (incluido en el extra de carreras).
- Una pantalla trasera para facilitar a los oponentes la detección del robot (incluida en el extra de carreras).
- Un soporte para la cámara (incluido en el extra de cámara).

A continuación, se detallan algunos consejos de impresión 3D generales y específicos de cada una de las piezas para facilitar el montaje y no desesperar en el intento.

Consejos generales

- No imprimir a una temperatura demasiado alta, de lo contrario el plástico se desparramará por los bordes y quedarán paredes irregulares, provocando entre otras cosas que los agujeros se cierren lo suficiente como para que luego no entren los tornillos o encajen las tuercas.
- Imprimir con PLA y un ventilador para enfriar las piezas rápidamente suele dar mejores resultados que con ABS.
- Hacer uso del parámetro “XY size compensation” de Slic3r (Print Settings->Advanced) facilita mucho la obtención de un buen acabado. Este parámetro da la tolerancia que se le indique para recortar la pieza en todo su contorno en el plano XY. Es muy útil para agrandar unas décimas de milímetro los agujeros sin necesidad de recurrir a limas o taladros.

Soportes de motores

Este diseño es una reproducción de los típicos soportes de micro motores de reductora metálica de Pololu. Se emplean dos tuercas y dos tornillos M2 por cada soporte para fijarlo al chasis del robot.

Las tuercas van encajadas a presión en los soportes, pero si no entrasen bien se puede recurrir a un soldador para calentarlas, fundiendo un poco el plástico para introducirlas. Es muy importante que la tuerca quede perpendicular al tornillo para no estropear de ninguno de los dos al atornillar el soporte.

Características de impresión:

- Sin soportes
- Altura de capa de 0,1 mm
- XY size compensation entre -0.1 y -0.2 mm

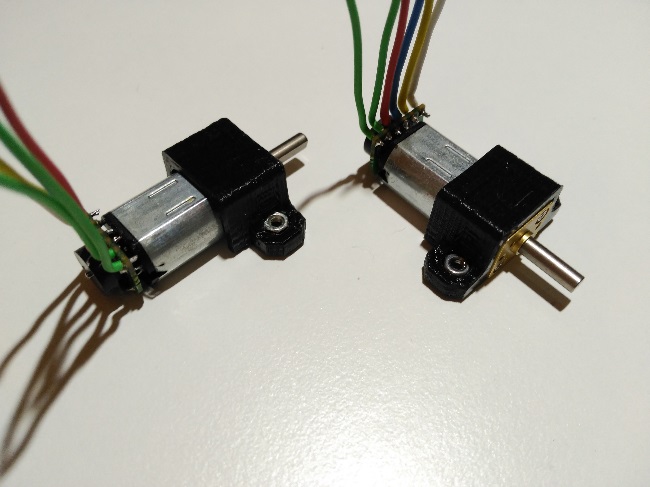
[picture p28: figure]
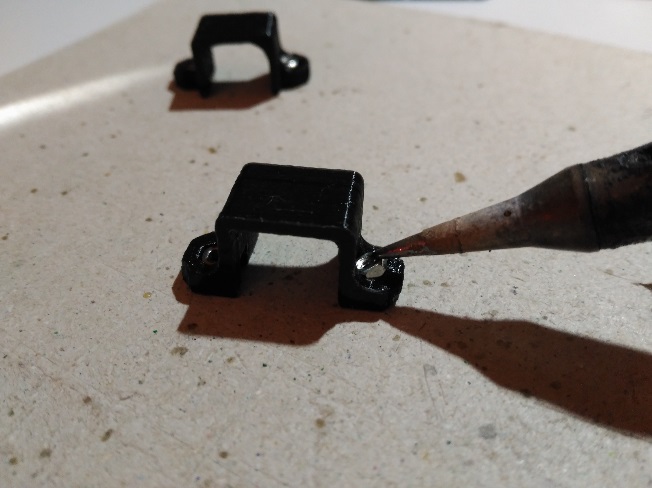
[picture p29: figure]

Soporte de sensores de distancia

Este soporte está pensado para encajar a presión tres sensores Sharp GP2Y0A y cualquier otro que presente la misma carcasa que éste. Va fijado al chasis con cuatro tuercas insertadas y cuatro tornillos.

Es una pieza bastante simple, y la altura de capa no es demasiado importante para su acabado, pero sí que es importante la utilización del parámetro “XY size compensation”, aproximadamente entre -0.1 y -0.15 mm, para no tener que recortar los agujeros con un cúter para meter los sensores a presión.

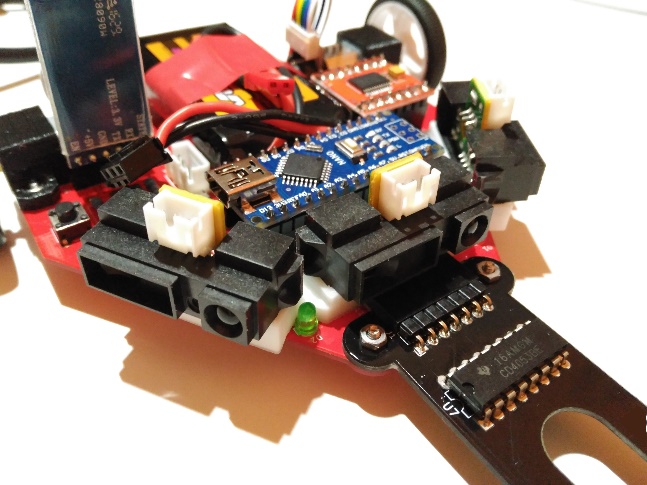
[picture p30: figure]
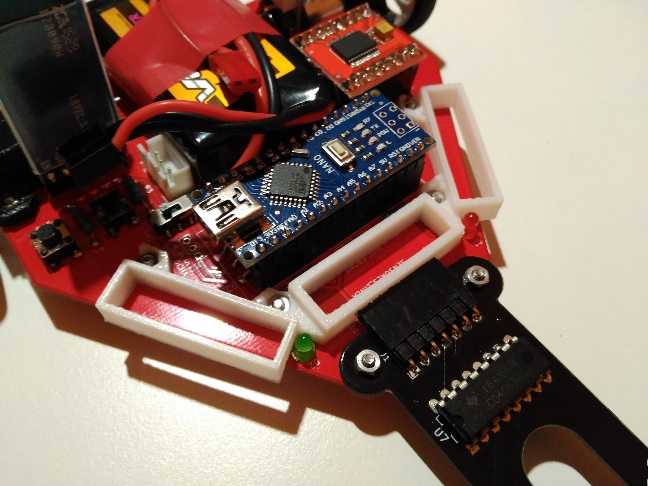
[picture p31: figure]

Pantalla trasera

Ésta es una simple pantalla blanca para que los oponentes puedan detectar con más facilidad al robot mediante infrarrojos y adelantarlo en carrera. Llevarla en carreras es obligatorio en la normativa actual de la LNRC, por lo que se ha decidido incluirla en el kit, pero no es necesario para que el robot funcione.

Su impresión no es crítica, pero es aconsejable establecer un valor de parámetro “XY size compensation” entre -0.05 y -0.1 mm. Aun así, se deberán calentar las tuercas para insertarlas en la pieza, con cuidado de no fundir el plástico demasiado y tapar el agujero. Va sujeto con un par de tornillos a la parte trasera del robot.

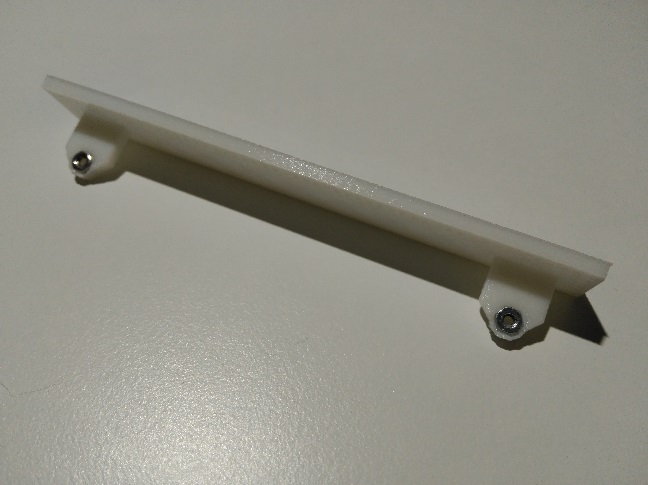
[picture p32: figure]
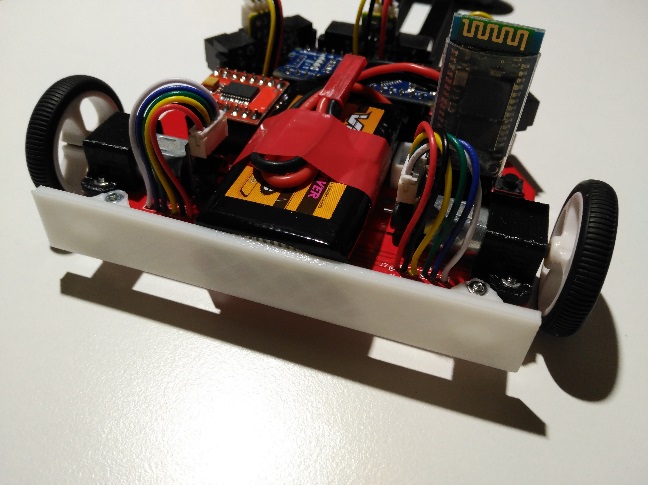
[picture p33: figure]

Soporte de cámara

Al igual que las demás piezas impresas, el soporte de la cámara va fijado mediante tuercas y tornillos M2 al chasis del robot, y las tuercas será necesario calentarlas para poder introducirlas en la pieza impresa.

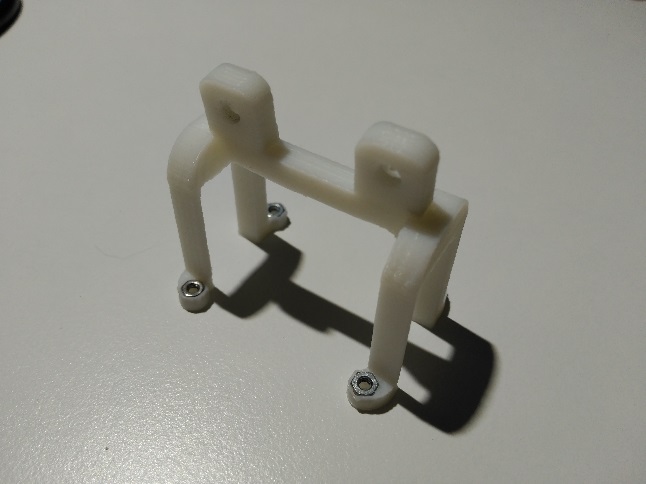
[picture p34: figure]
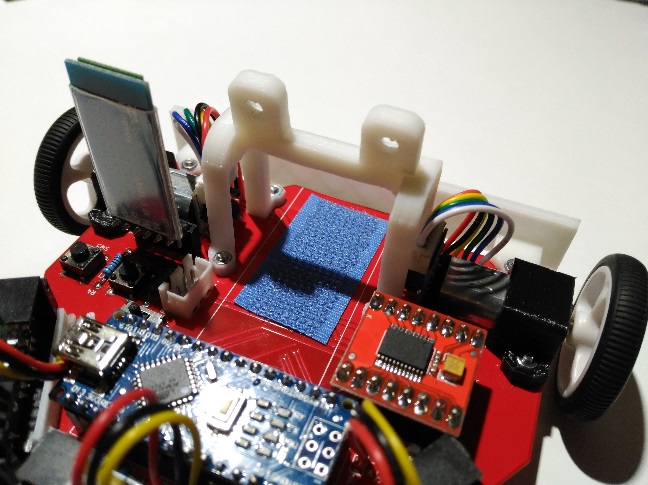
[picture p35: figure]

El primer diseño incluía una cámara TSL1401CL de APTech, pero se ha dado opción a poder poner otras equivalentes de otros distribuidores como Aliexpress. Sus diseños se diferencian en la posición de los orificios de la cámara y en la manera de atornillarla (la de APTech por delante; la de Aliexpress por detrás), aunque ambos utilizan los mismos tornillos y tuercas M3.

También se ha añadido un soporte regulable (diseñado por @jbabio) para ajustar la cámara de Aliexpress con diferentes inclinaciones, muy útil para las pruebas en entornos con luz variable. En caso de implementar este soporte se necesitarán 2 tornillos adicionales M2x8mm.

Características de impresión:

- Sin soportes
- Altura de capa de 0,1 mm
- XY size compensation entre -0.05 y -0.1 mm

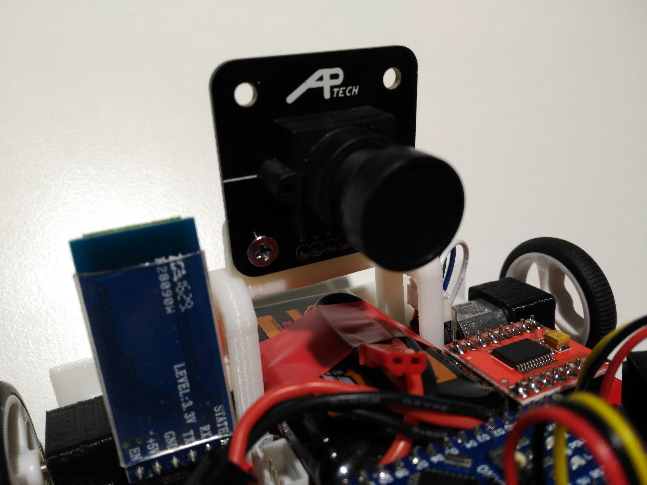
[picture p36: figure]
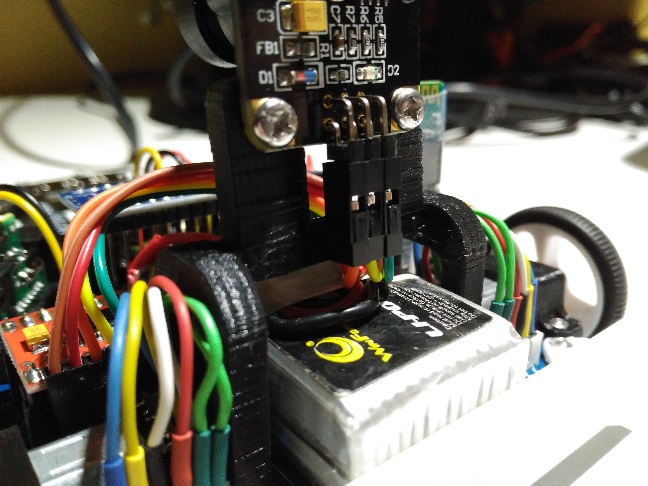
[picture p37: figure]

Visera para los sensores de distancia

A veces ocurre que algún sensor de distancia está colocado con una inclinación tal, que llega a detectar el suelo como si fuera un obstáculo o un oponente, por lo que sería necesario apantallar la parte inferior del sensor para evitar estas falsas detecciones.

Tras haber hecho las primeras pruebas, no ha sido necesario apantallar los sensores, pero se incluye este diseño en el proyecto de Github por si a alguien le fuese de utilidad. Esta visera va encajada a presión en la parte frontal de los sensores de distancia.

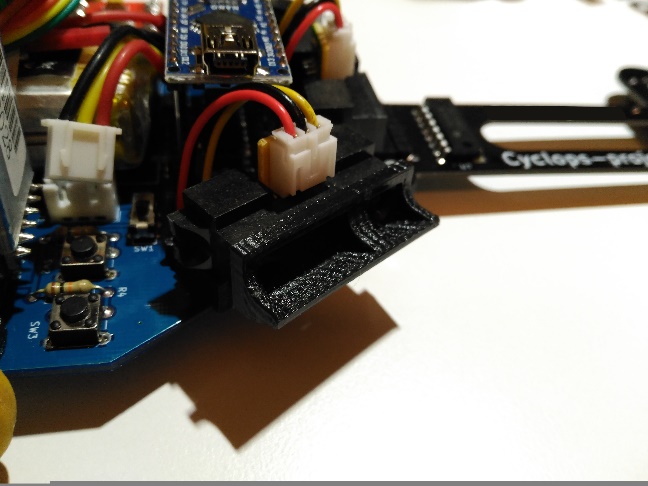
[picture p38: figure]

Características de impresión:

- Sin soportes
- Imprimir relleno antes que los perímetros
- Imprimir perímetros interiores antes que el exterior
- Altura de capa de 0,1 mm
- XY size compensation entre -0.05 y -0.1 mm

Consejos de impresión para las piezas del robot Rubén Espino San José

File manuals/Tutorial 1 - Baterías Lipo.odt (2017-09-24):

BATERÍAS LIPO

Una de las mayores limitaciones de los robots, al igual que de cualquier aparato electrónico, autónomo y dotado de movimiento, es el sistema de alimentación. A medida que se desarrollan baterías con mayor capacidad de carga y descarga, menor peso y mayor duración, se favorece el desarrollo de este tipo de sistemas.

Las baterías de litio han supuesto una revolución en la tecnología moderna, y hoy en día prácticamente ni se plantea el hecho de incorporar otro tipo de baterías en sistemas autónomos como los robots de competición en los cuáles se basa este proyecto. En general, cualquier batería de litio proporciona una alta capacidad de descarga, pero son las baterías Lipo (Litio-Polímero) las más demandadas en robots de competición por sus excelentes cualidades.

Las baterías de Litio-Polímero son ideales para alimentar la electrónica alojada en un robot móvil porque proporcionan una alta capacidad de descarga, pudiendo llegar a aportar decenas de amperios a su salida en función de sus parámetros. Además, son las baterías con mejor relación de capacidad de descarga respecto al peso si las comparamos con otras que pueden utilizarse en radiocontrol o robótica, como las de NiCd (Níquel-Cadmio), NiMH (Níquel-Metal Hidruro) y Pb (Plomo).

Estas baterías se dividen en celdas de 3,7V, aunque llegan a alcanzar una tensión de 4,2V cuando están totalmente cargadas. Así, las Lipo presentarán una tensión máxima siempre múltiplo de 4,2V, según el número de celdas o segmentos: 4,2V (1S), 8,4V (2S), 12,6V (3S)...

En la siguiente imagen puede verse una batería Lipo y los dos conectores de los que dispone: el conector de carga (el blanco) y el de potencia (el rojo). El primero de ellos es un modelo común en las baterías Lipo, mientras que el segundo suele cambia en función de la corriente que sea capaz de aportar la batería para no quemarlo.

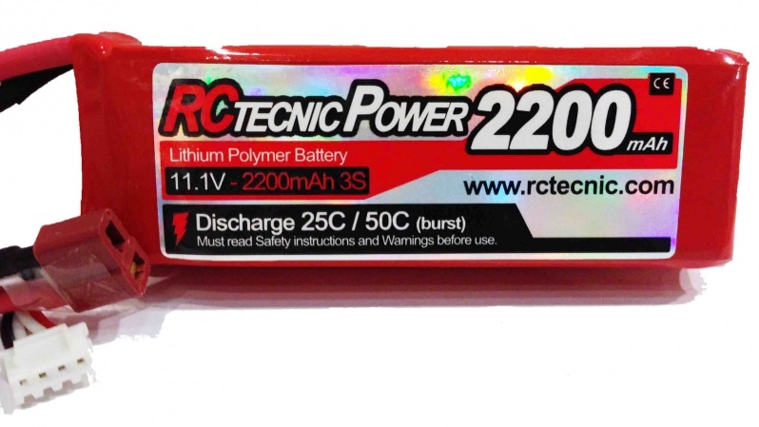
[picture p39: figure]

# Cálculo de parámetros

Utilizando la batería anterior como ejemplo, se va a proceder a explicar qué significa cada uno de sus parámetros y cómo hacer los cálculos para saber sus características y si es la adecuada para el robot en el que se pretende embarcar:

- 11.1V es la tensión de la batería cuando todas sus celdas están cargadas a 3,7V.
- 2200mAh es la capacidad en mAh de la batería.
- 3S es el número de celdas o segmentos de la batería.
- 25C es la constante de descarga de la batería en continua.
- 50C es la constante de descarga de la batería en pico.

La corriente que es capaz de aportar la Lipo se calcula multiplicando la capacidad de la batería por la constante de descarga. De esta manera tendremos la descarga en continua y en pico:

2000 mAh · 25 C = 55 A en continua

2000 mAh · 50 C = 110 A en pico

Y la duración de la batería, descargando a la corriente máxima en continua que acaba de calcularse, viene dada por el resultado de dividir 60 minutos entre la constante de descarga en continua:

60 min / 25 C = 2 min 24 s

Mediante una regla de tres inversa, si el cálculo del sistema hubiera dado 5A de consumo en continua, la autonomía del robot sería de:

(2 min 24 s) · 55 A / 5 A = 26 min 24 s

Podría pensarse que una batería de más capacidad aportaría una mayor autonomía al sistema, pero no siempre es cierto. Una mayor capacidad implica cargar con más peso, y por tanto un mayor consumo, por lo que es importante encontrar una relación de compromiso entre el peso de la batería y la capacidad de la misma, para obtener la mayor autonomía posible.

# Mantenimiento

Aunque las ventajas de las baterías Lipo frente al resto las hacen más adecuadas para su empleo en robótica de competición, también son de las más peligrosas y requieren de un buen uso y mantenimiento que se resume en los siguientes puntos:

- Utilizar un cargador especial balanceado como el imax b6 de la siguiente imagen, que sirve para baterías de Lipo, NiCd, NiMH, Pb (plomo), etc. No es necesario cargar siempre de forma balanceada, pero sí a menudo para que no se descompensen las celdas de la batería y se mantengan a la misma tensión. En caso de utilizar el modo de carga balanceado será necesario emplear los dos conectores para que se equilibren las celdas. El de potencia realiza una carga general, mientras que el conector de carga balanceada monitoriza y compensa la tensión de las celdas.

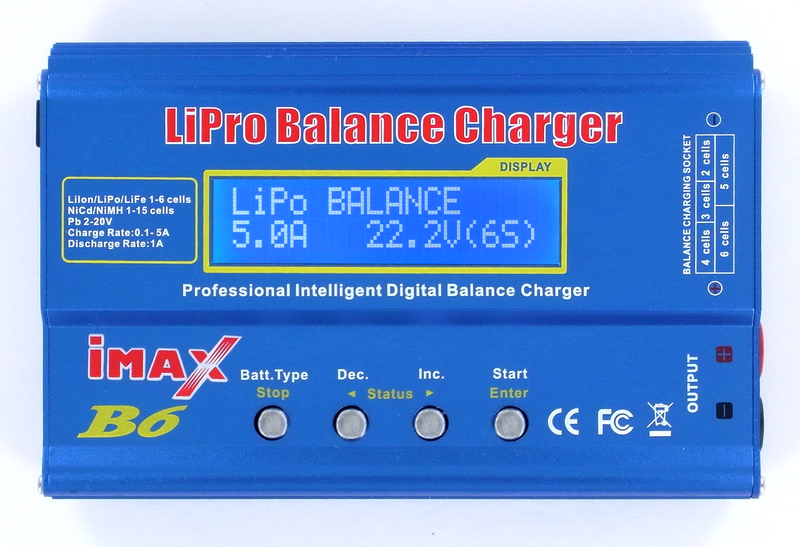
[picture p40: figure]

- Conservar las baterías a 3,8V cada celda mediante el modo Lipo Storage cuando no se vayan a utilizar durante varias semanas. A esta tensión las celdas se mantienen indefinidamente sin necesidad de revisarlas, mientras que si se dejan completamente cargadas pueden llegar a estropearse.
- No cortocircuitar la batería ni golpearla porque puede llegar a arder o explotar.
- No permitir que las celdas bajen de 3V cada una, de lo contrario se estropearán e hincharán.
- Es aconsejable monitorizar la batería durante su uso con un divisor resistivo hacia una entrada de ADC del microcontrolador y/o poner una alarma en el conector de carga que avise cuando alguna de las celdas tenga la tensión baja, de aproximadamente menos de 3,8V.

Tutorial de baterías Lipo Rubén Espino San José

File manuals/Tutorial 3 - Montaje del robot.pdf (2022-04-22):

Tutorial de montaje del robot | Rubén Espino San José

# Montaje de Cyclops-Project

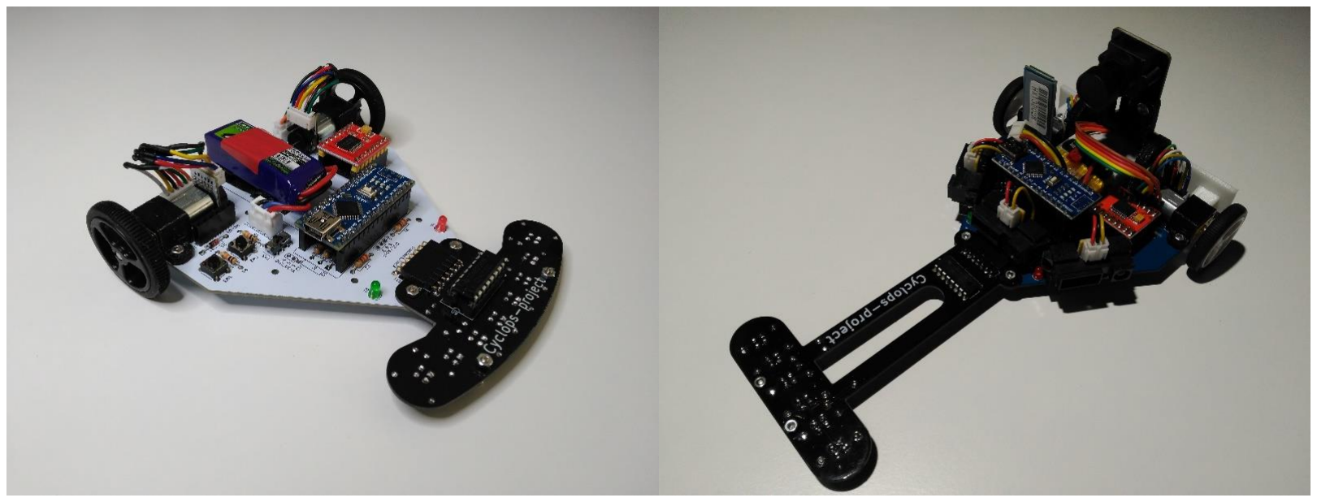
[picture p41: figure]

HERRAMIENTAS NECESARIAS

- Soldador y estaño
- Destornillador de estrella (para tornillos M2 y M3)
- Alicate (aconsejable de punta fina, para sujetar las tuercas M2)
- Cortacables
- Cúter
- Polímetro

HERRAMIENTAS ÚTILES, PERO NO IMPRESCINDIBLES

- Gafas de protección (la conjuntivitis, la sequedad en los ojos y la posibilidad de que salte la resina del estaño no suelen hacer mucha gracia)
- Soporte con pinzas (viene bien para sujetar PCBs o motores a la hora de soldar)
- Pelacables (sustituible por el cortacables)

NOTAS IMPORTANTES:

- Se ruega encarecidamente seguir este tutorial, ya que existen numerosos detalles y pasos secuenciales que deben seguirse para evitar posibles errores durante el montaje del kit, así como diferencias entre distintas versiones de las PCBs
- Para guiarse mejor, pueden encontrarse los diseños de las PCBs y del ensamblado del robot en FreeCAD, en la carpeta hw/FreeCAD
- No fiarse de los colores de las fotos, ya que pueden verse alterados por diversos motivos, dando lugar a confusión en la colocación de las resistencias
- En caso de tener la versión 2 de la PCB principal, ésta llevará por su cara posterior la inscripción “Main_board_V2”

Placa principal

Materiales necesarios:

- PCB principal
- Diodo 1N4001
- 2x resistencia 10k
- 2x resistencia 1k
- 2x resistencia 220 ohmios
- Resistencia 82k
- Resistencia 120k
- Led rojo
- Led verde
- Conector batería
- Conmutador
- 2x pulsador
- Expansor I2C PCF8574P
- Zócalo DIP de 16 patillas
- 2x conector hembra 15 pines
- 2x conector hembra 8 pines
- Conector hembra 4 pines tumbado

Todos los materiales que se necesitan aparecen en la siguiente foto, pero el conversor DC-DC, la Arduino Nano y el driver de motores se montarán en un apartado posterior.

La correspondencia entre los componentes y sus nombres puede verse en el archivo hw\Kicad\Main_board_V2\Mainboard.ods.

Para reconocer los valores de las resistencias se puede hacer uso de un polímetro o del código de colores de las resistencias. (https://www.inventable.eu/2015/06/04/como-se-leen-los-colores-de-las-resistencias/) En función de si tienen 4 o 5 bandas de color, las 3 o 4 primeras bandas corresponderán al valor de la resistencia, respectivamente.

Detalles a tener en cuenta para soldar los componentes:

- Si tienes dos diodos, normalmente uno negro (1N4001) y otro naranja (1N4148), éste último forma parte del extra de bluetooth que se montará más adelante
- El lado plano de cada led (patilla más corta) se corresponde con el pin cuadrado (orientado hacia el interior de la PCB)
- Prestar especial atención a la polaridad o posición del diodo, del expansor I2C (y su zócalo) y del conector de la batería, que aparecen indicadas en la serigrafía de la PCB. En caso de montar el expansor I2C del revés, es probable que se estropee
- No confundir el expansor I2C con el multiplexor de la placa de sensores, que tiene el mismo encapsulado. Revisar el código del componente antes de montarlo encima del zócalo, que debe soldarse previamente a la PCB
- El conmutador y los pulsadores son reversibles, no importa cómo se coloquen

En la siguiente imagen pueden verse los componentes soldados, excepto los conectores hembra verticales, que son los últimos en soldarse por ser los componentes más altos.

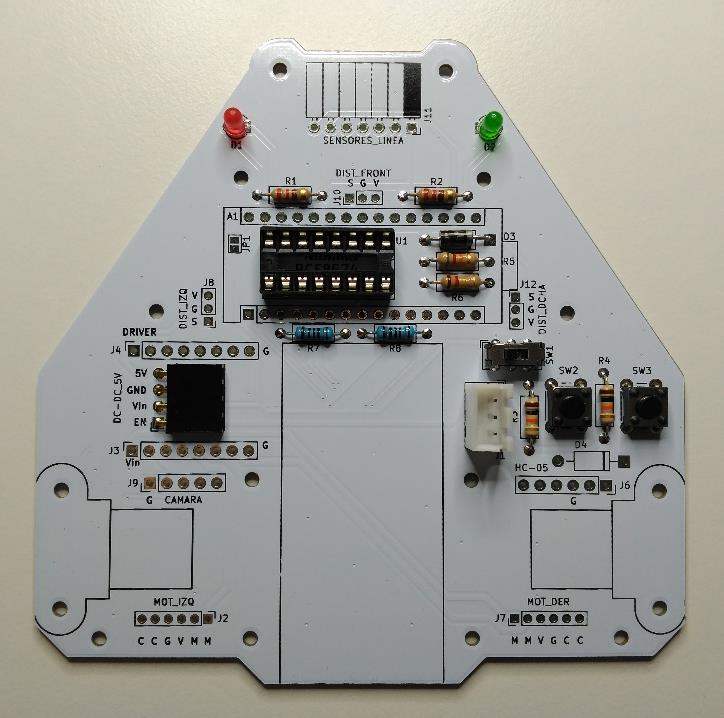
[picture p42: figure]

Por último, se sueldan los conectores de la Arduino y del driver, con cuidado de que queden lo más vertical posible, y se monta el expansor I2C sobre su zócalo:

DC-DC, Arduino y driver de motores

El siguiente paso consiste en preparar la Arduino Nano, el conversor DC-DC y el driver de motores.

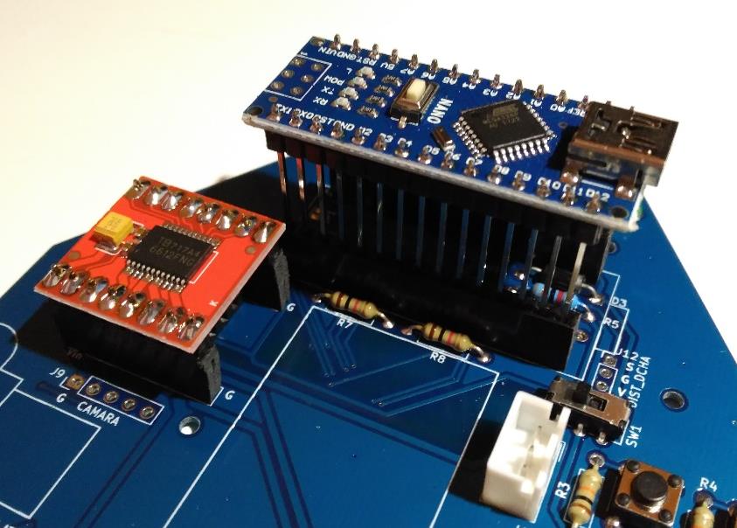
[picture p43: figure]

- Arduino Nano: si estás pensando en poner sensores de distancia en el chasis, lo mejor es soldar en la Arduino los pines largos para que el sensor de distancia derecho no obstruya el conector mini USB de la Arduino y no haya que estar desconectándola siempre que se quiera cargar un programa. Si no, siempre se puede poner los pines estándar que se ven en la parte derecha de la imagen.
- No confundir los agujeros de las esquinas de la Arduino con más pines, de lo contrario podría quedar la tira de pines desplazada y tocaría cambiarla.
- Driver de motores: en este caso se necesitan los dos conectores estándar de 8 pines.

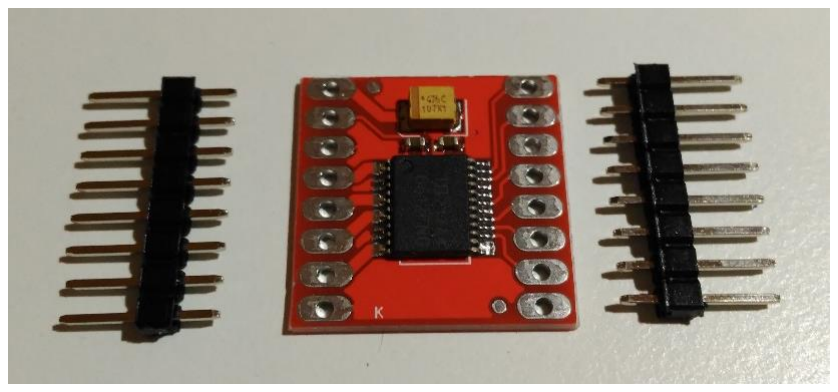
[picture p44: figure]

- Conversor DC-DC: se ha decidido introducir un conversor DC-DC de 5V para alimentar todo el robot debido a la gran cantidad de componentes que contiene, pero en principio no es necesario. Si no se desea incluir, basta con no ponerlo y soldar los pines del jumper JP1 que hay bajo la Arduino para utilizar su propio regulador de 5V.
- En caso de utilizar el DC-DC del que dispone el kit, se debe seguir el siguiente procedimiento:
- Realizar un corte con un cúter en la pista que indica la flecha roja en la imagen derecha. Esto evitará que la tensión de salida se pueda regular con el potenciómetro que lleva incorporado el DC-DC.
- Comprobar con un polímetro que ha dejado de haber continuidad entre los pines indicados con las flechas azules. Se puede hacer con el test de continuidad, viendo que no pita el polímetro; o se puede intentar medir la resistencia, cuyo valor tiene que ser tan grande que el polímetro no pueda medirlo.
- Soldar el jumper que hay junto a la serigrafía de “5V”, indicado con una flecha amarilla en la imagen derecha.

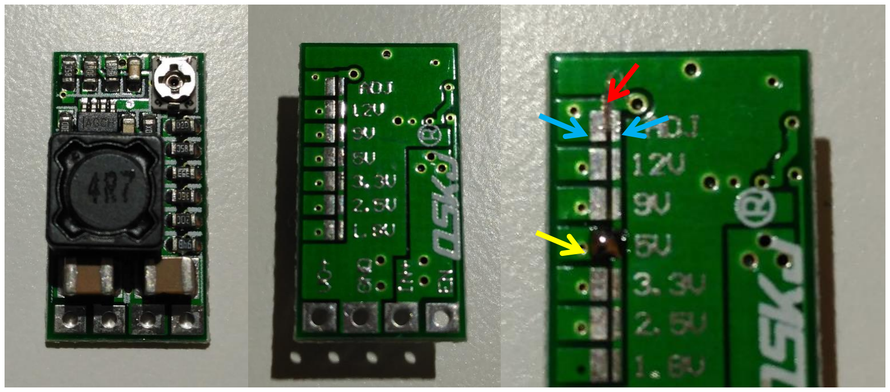
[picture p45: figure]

- Soldar el conector macho acodado de 4 pines por la tarde trasera, como muestra la imagen inferior.
- Conectar el DC-DC lateralmente debajo del driver de motores.

Placa de sensores

Materiales necesarios para la placa Sensors_board (versión velocista):

- PCB de sensores
- 6x CNY70
- 6x resistencia 10k
- 3x resistencia de 82 ohmios (27 ohmios en el caso de algunas copias de CNY70)
- Multiplexor CD4053
- Zócalo DIP de 16 patillas
- 4x tuerca M2
- 2x tornillo M2x10mm

Materiales necesarios para la placa Sensors_board_V2 (versión rastreador):

- PCB de sensores
- 8x CNY70
- 8x resistencia 10k
- 3x resistencia de 82 ohmios
- Multiplexor CD4052
- Zócalo DIP de 16 patillas
- 4x tuerca M2
- 2x tornillo M2x10mm

La correspondencia entre los componentes y sus nombres puede verse en el archivo hw\Kicad\ Sensors_board\ Sensors_board.ods o en hw\Kicad\ Sensors_board_V2\ Sensors_board.ods. Revisar los consejos de montaje de la siguiente página antes de soldar los componentes.

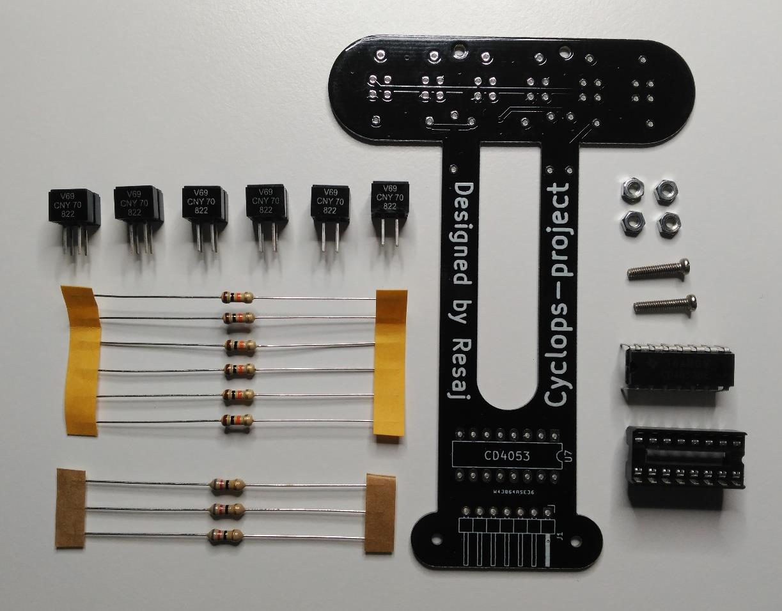
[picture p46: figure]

La razón por la que se eligen 27 u 82 ohmios para las resistencias asociadas a los CNY70 es la diferencia entre sensores. Los CNY70 originales necesitan resistencias de 82 ohmios, mientras que los comprados en algunas tiradas de Aliexpress pueden ser copias que difieren en algunos parámetros. Haciendo pruebas con esas copias se ha llegado experimentalmente a un valor de 27 ohmios para las resistencias de esos sensores, pudiendo variar para diferentes tiradas de copias de CNY70.

Una de las diferencias más notables entre esas versiones de sensores es que las ventanas del emisor y del receptor son totalmente planas en los originales, mientras que en las copias que hemos encontrado sobresalen un poco, como puede verse en alguna de las imágenes que vienen a continuación.

Si has encargado el kit en vez de hacerlo tú mismo/a, éste vendrá directamente con las resistencias que necesitas para los sensores que se incluyen.

Consejos para soldar los componentes de la PCB de sensores (válido para ambas versiones de Sensors_board):

- Comenzar soldando las resistencias y el zócalo del multiplexor. Prestar atención a la posición del zócalo, indicada en la serigrafía, para no colocarlo del revés.
- Soldar los CNY70 con la serigrafía de los componentes mirando hacia la parte trasera del robot, como se muestra en la siguiente imagen.

Hay que tener mucho cuidado al soldar los CNY70 para no quemar el led emisor con el calor, pero a veces pasa, por lo que en el kit se incluye algún sensor de repuesto. Uno de los trucos para no quemarlos consiste en dejarlos enfriar entre la soldadura de cada uno de sus pines.

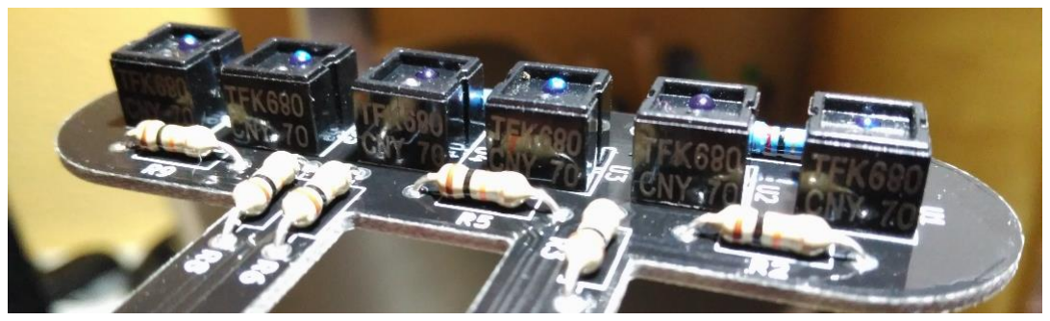
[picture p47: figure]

- Colocar el multiplexor en el zócalo. Revisar el código del multiplexor antes de montarlo para no confundirlo con el expansor I2C del chasis principal, ya que tienen el mismo encapsulado. Y revisar de nuevo la posición sobre el zócalo para no colocarlo del revés.
- Ayudarse de destornillador y alicates para poner los tornillos de apoyo con una tuerca por cada lado de la PCB. La distancia adecuada entre los sensores y el suelo deberá ser de 1 mm aproximadamente, ya que alejarlos demasiado puede provocar interferencias de luz externa y entre los propios sensores. No es aconsejable forzar demasiado los tornillos y tuercas M2, ya que podría estropearse la rosca.

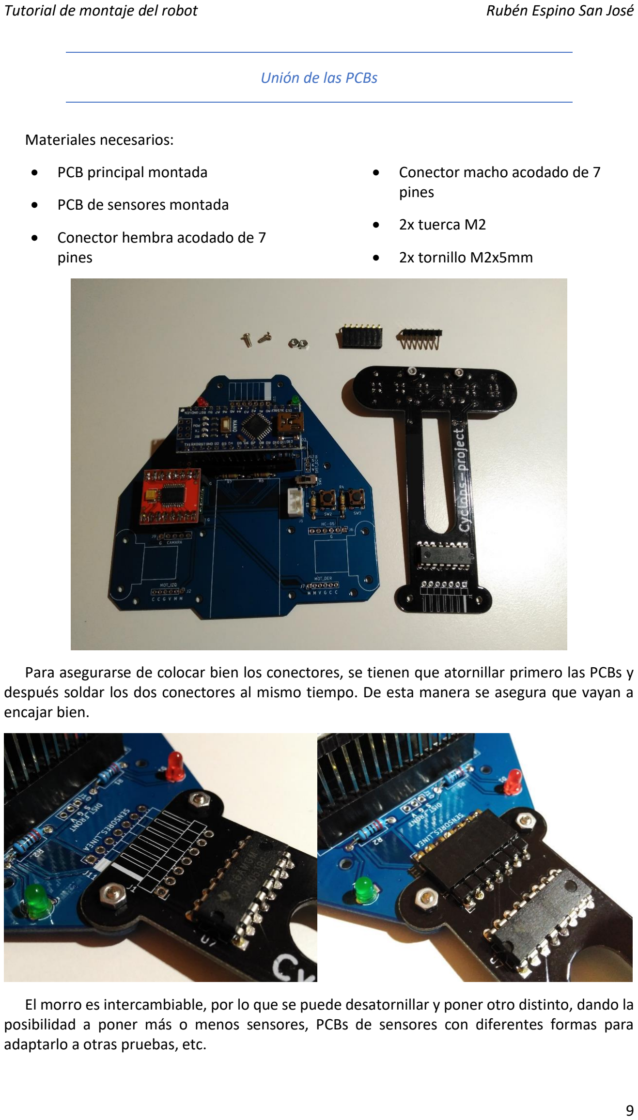
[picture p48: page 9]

Unión de las PCBs

Materiales necesarios:

- PCB principal montada
- PCB de sensores montada
- Conector hembra acodado de 7 pines
- Conector macho acodado de 7 pines
- 2x tuerca M2
- 2x tornillo M2x5mm

Para asegurarse de colocar bien los conectores, se tienen que atornillar primero las PCBs y después soldar los dos conectores al mismo tiempo. De esta manera se asegura que vayan a encajar bien.

El morro es intercambiable, por lo que se puede desatornillar y poner otro distinto, dando la posibilidad a poner más o menos sensores, PCBs de sensores con diferentes formas para adaptarlo a otras pruebas, etc.

Motores

Debido a los problemas para encontrar micro motores 10:1 HP con encoders en cuadratura fiables y económicos, se han probado varias opciones que se detallan a continuación.

Materiales necesarios:

- Opción 1: encoders ya montados en los
motores y cables soldados en chasis
- 2x micro motor 10:1 HP con
encoder | magnético | en
cuadratura
- 2x cable de conexión de motor y encoder
- 2x soporte micro motor
- 2x rueda
- 4x tuerca M2
- 4x tornillo M2x5 mm
- Opción 2: motores y encoders separados y sin cablear, con conector en chasis
- 2x micro motor 10:1 HP
- 2x encoder magnético en cuadratura
- 2x imán para encoder

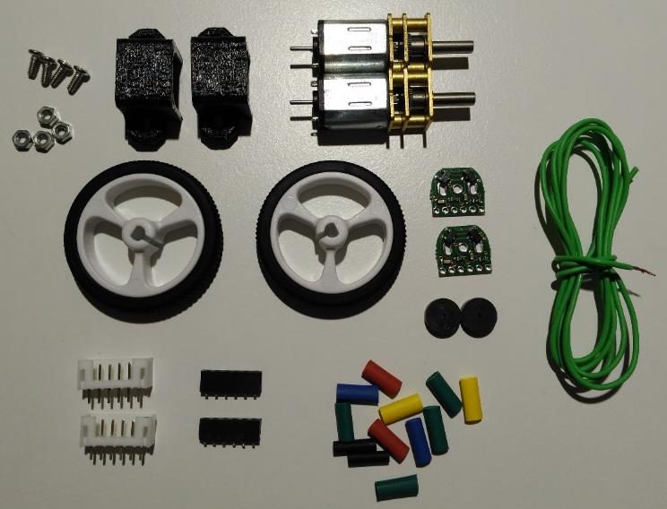
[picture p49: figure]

- 2x conector macho de
6 pines con paso 2 mm
- 2x conector hembra de
6 pines con paso 2mm
- Cable
- Termorretráctil
- 2x soporte micro motor
- 2x rueda
- 4x tuerca M2
- 4x tornillo M2x5 mm

- Opción 3: motores con encoders cableados, con conector en chasis
- 2x micro motor 10:1 HP
con encoder magnético
en | cuadratura | ya
cableado
- 2x conector macho de 6
pines con paso 2 mm
- 2x soporte micro motor
- 2x rueda
- 4x tuerca M2
- 4x tornillo M2x5 mm
- Opción 4: motores con encoders, con conector en ambos lados y cables ya montados
- 2x micro motor 10:1 HP
con encoder magnético
en cuadratura
- 2x conector macho de
6 pines con paso 2 mm
- 2x bus de cables con
conectores
- 2x soporte micro motor
- 2x rueda
- 4x tuerca M2
- 4x tornillo M2x5 mm

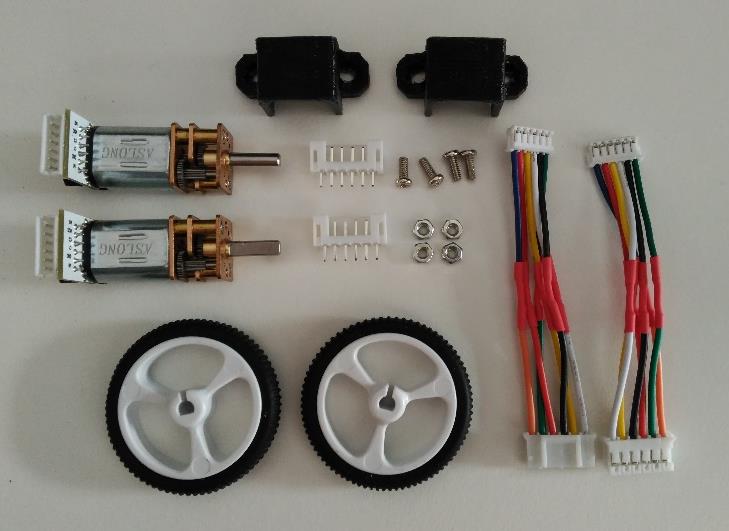
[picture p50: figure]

Como se han propuesto diferentes opciones, no se ha marcado la orientación del posible conector en la serigrafía de la PCB, pero sí los pines correspondientes, que se tendrán en cuenta más adelante para conectar los motores y encoders de las opciones 1 y 2 correctamente. En el caso de que vayan conectores montados en el chasis, se puede empezar por soldarlos como muestra la siguiente imagen:

En el caso de que los motores y los encoders no estén soldados, estos son los pasos a seguir para montarlos y cablearlos:

- Sujetar el motor y soldar la PCB de los sensores de efecto hall en su parte posterior. Observar que la patilla positiva del motor se ha soldado al pad M1 del encoder por seguir un orden, aunque realmente se puede modificar la dirección del motor por software si se monta invertido. Tener especial cuidado en montar la PCB centrada para que el eje trasero del motor no roce con la PCB.

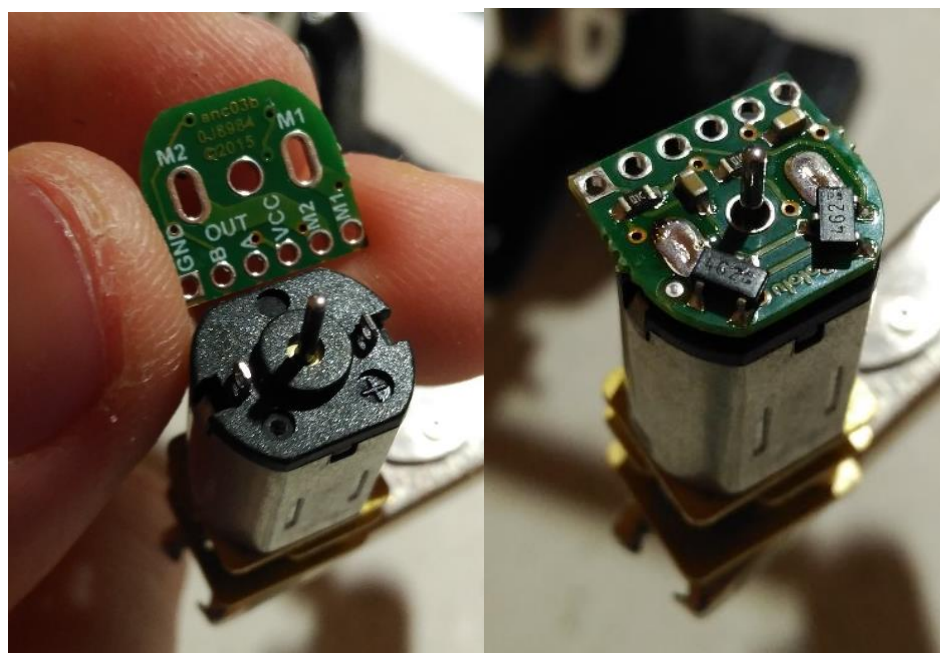
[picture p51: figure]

- Insertar el disco de los imanes en el eje trasero. Si se presiona hasta el fondo, el rotor tiene el juego suficiente para que al dejar de presionar el disco retroceda hasta una buena posición para que lo detecten los sensores, pero sin tocarlos.

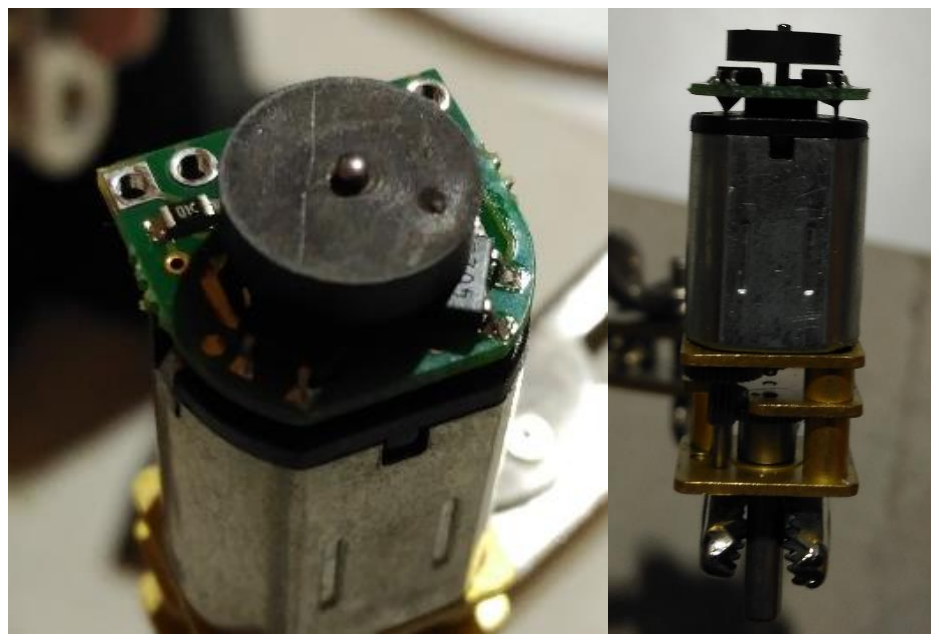
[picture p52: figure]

- Cortar 6 cables de 5 cm para cada motor, pelarlos y soldarlos en la PCB de los encoders. Utilizar diferentes colores suele ser útil para identificar después a qué cable corresponde cada pin

Antes de soldar los posibles conectores a los cables de los motores, es mejor atornillar los motores al chasis. Para ello, se introducen las tuercas M2 en los soportes de los motores (si es necesario, con un poco de ayuda calentando las tuercas con un soldador) y se atornillan al chasis, amordazando los motores. Es necesario colocar bien las tuercas para que no queden torcidas, ya que esto puede provocar que se estropee su rosca o la del tornillo.

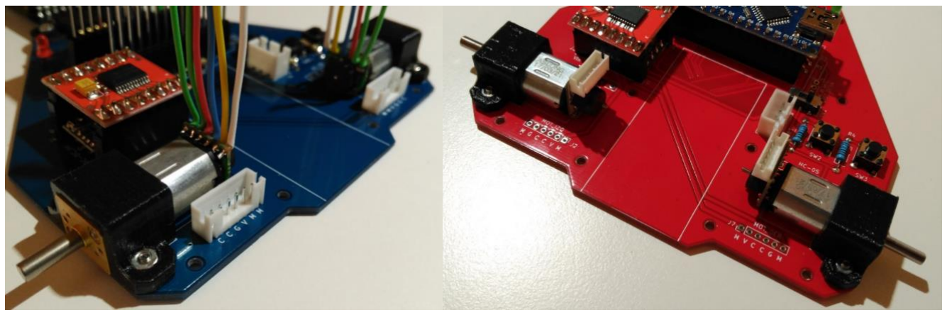
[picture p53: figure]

Para finalizar el montaje de los motores, éstos deben conectarse al chasis. Pero antes de conectarlos hay que tener en cuenta la correspondencia de pines, puesto que en cada tipo de PCB de encoder suelen tener un orden diferente. En las opciones 3 y 4 los conectores ya tienen conectados los pines por orden. En total hay 6 pines:

- 2 pines correspondientes a las patillas del motor. No importa intercambiarlos, se puede modificar su orden por software
- 2 pines correspondientes a las señales de los dos encoders en cuadratura. No importa intercambiarlos, se puede modificar su orden por software
- 1 pin de Vcc (5V) para alimentación de los sensores de efecto hall
- 1 pin de GND para referenciar la alimentación de los sensores de efecto hall

Por otra parte, en la PCB del chasis están marcados los pines correspondientes:

- M: dos pines para el motor
- C: dos pines para las señales de los encoders
- V: pin de 5V para la alimentación de los sensores de efecto hall
- G: pin de GND para referenciar la alimentación de los sensores de efecto hall

A continuación, se detalla la conexión para cada una de las opciones señaladas.

Si el kit de motores lleva el conector en la PCB de los encoders, se pueden cortar los cables de 5 cm y soldarlos a la PCB, como muestra la siguiente imagen y teniendo en cuenta la correspondencia de pines, que no quedarán ordenados como en la imagen.

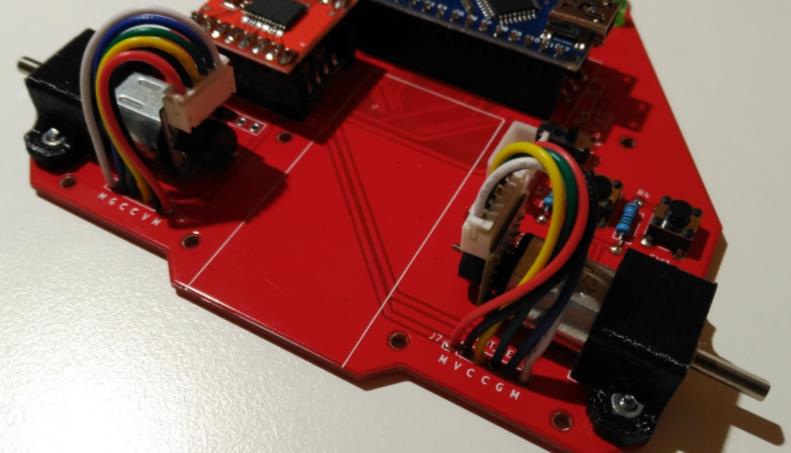
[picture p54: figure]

En el caso de que el kit no lleve los conectores soldados a los motores ni a los cables, el procedimiento será el siguiente:

- Se introduce un trozo de termorretráctil en cada cable, alejándolos del extremo que se va a soldar para que no se contraigan con el calor.
- Se enchufa el conector para los cables al de la PCB para mantenerlo sujeto.
- Se suelda cada uno de los pines con su cable correspondiente, como muestra la siguiente imagen, pero no tiene por qué ser el mismo orden.

- Se espera a que se enfríen las soldaduras, se desenchufa el conector y se colocan los trozos de termorretráctil cubriendo las soldaduras. En la siguiente imagen aparece el conector enchufado, pero es aconsejable hacer el siguiente paso con él desenchufado.

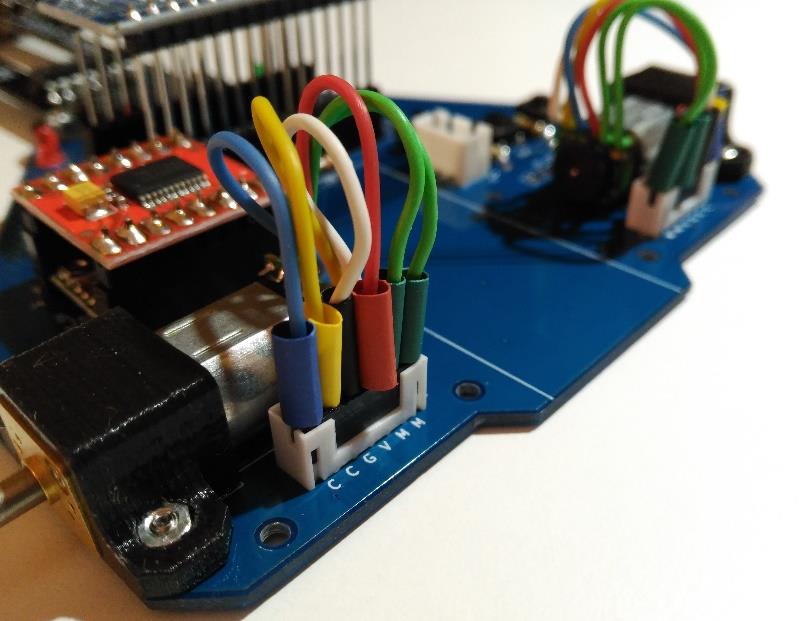
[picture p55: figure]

- Se calientan los trozos de termorretráctil para que se retraigan y protejan las soldaduras, previniendo posibles cortocircuitos. Se vuelve a enchufar el conector y queda listo para funcionar.

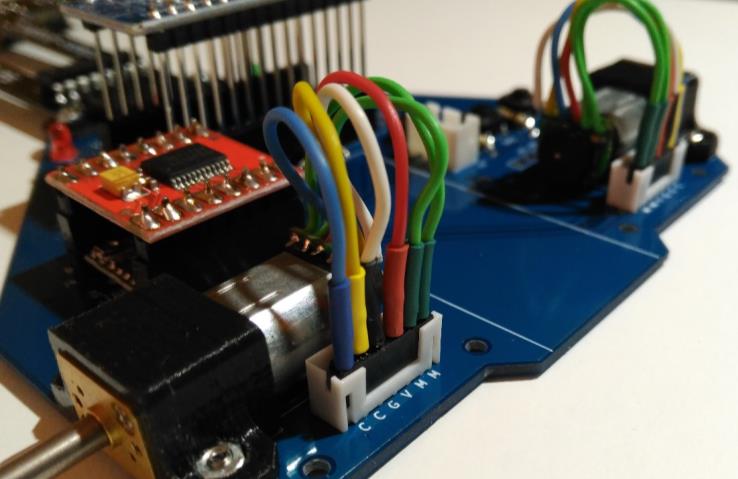
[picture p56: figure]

- Por último se colocan las ruedas insertándolas a presión en los ejes de los motores.

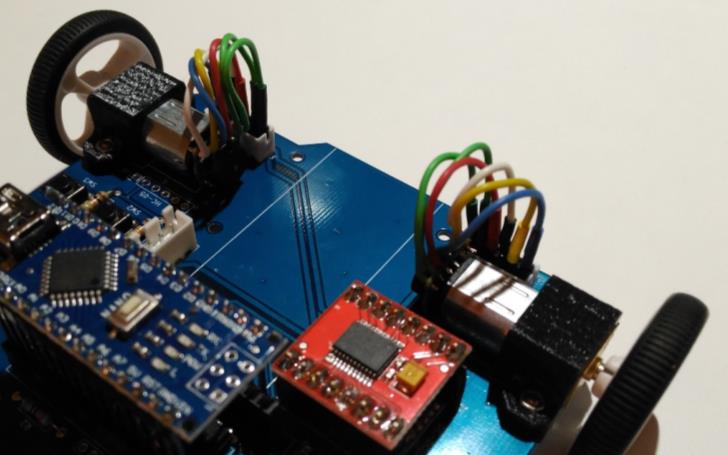
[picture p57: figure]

Las opciones 3 y 4 tienen el cableado ya preparado para conectarlo, pero en la opción 3 los motores vienen con un cable demasiado largo, que se puede acortar de la siguiente manera:

- Cortar los últimos 5 cm del extremo del cable
- Quitar imán del encoder, anotar los pines de la PCB del encoder con sus colores de cable correspondientes, pelar mínimamente los cables del bus de 5 cm con el conector y desoldar el bus de cables del encoder

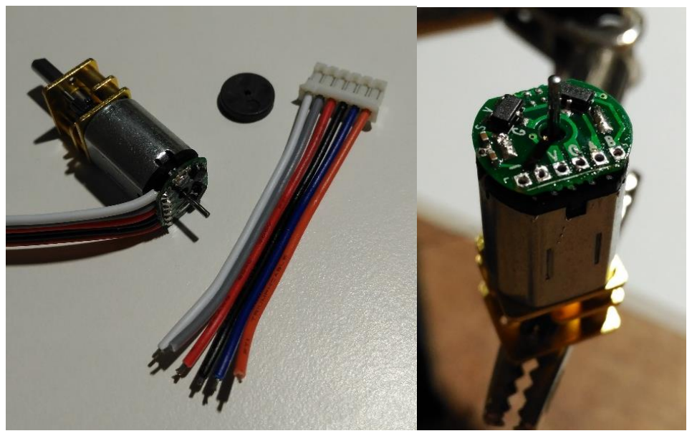
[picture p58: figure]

- Soldar los cables del bus sobre los pines de la PCB del encoder siguiendo el orden de colores inicial

Batería

Materiales necesarios:

- Batería lipo 2S
- Velcro adhesivo

El velcro adhesivo es muy útil para fijar la batería de una manera simple y segura. Para ello recomiendo pegar la parte suave del velcro a la batería, y una vez esté pegada, poner encima el lado más duro del velcro y colocar la batería sobre el robot. De esta manera la posición del velcro quedará justo donde tiene que ir, y no desplazada.

Bluetooth

Materiales necesarios:

- Bluetooth HC-05
- Conector hembra vertical de 6 pines
- Diodo 1N4148 (en caso de tener la Main_board_V2)

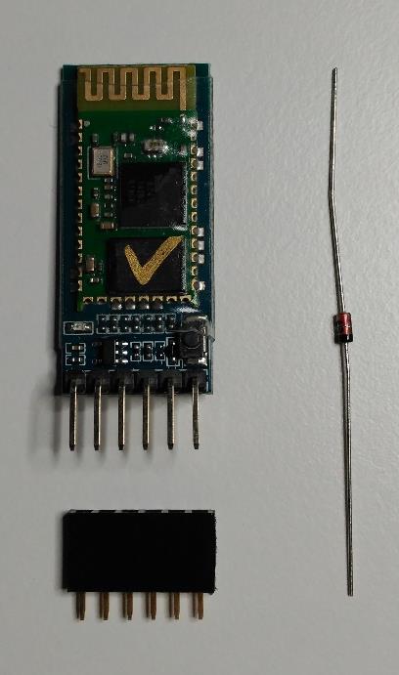
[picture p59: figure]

El diodo 1N4148 (típicamente naranja) corresponde al D4 indicado en la serigrafía y que queda justo por delante del bluetooth.

El conector de 6 pines se debe soldar justo delante del motor derecho del robot, y el bluetooth ha de pincharse en el conector con la cara superior mirando hacia la parte trasera del robot, como se puede ver en las siguientes imágenes:

Sensores de distancia

Materiales necesarios:

- Sensor GP2Y0A21
- 2x sensor GP2Y0A41
- 3x cable sensor Sharp
- Soporte de sensores de distancia
- 4x tuerca M2
- 4x tornillo M2x5mm

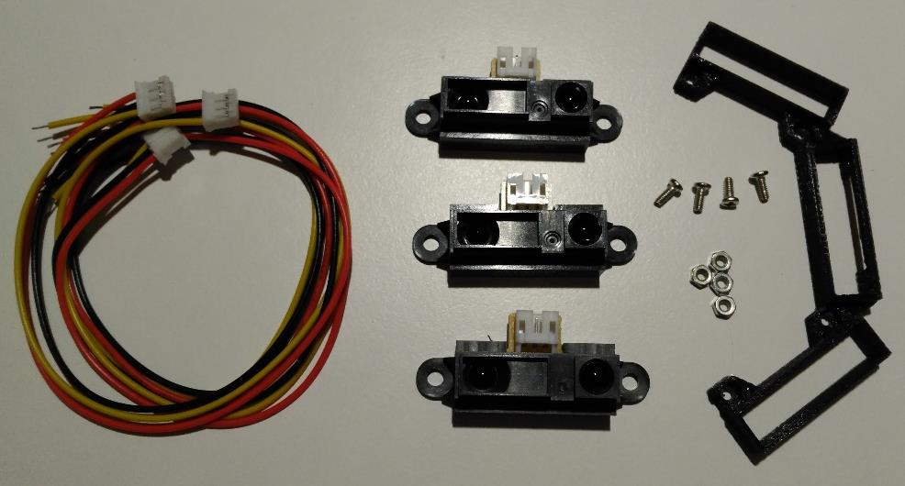
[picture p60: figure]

Pasos a seguir:

- Cortar las orejas de los sensores de distancia. No van a ir sujetos con tornillos, sino encajados directamente sobre el soporte y bastante juntos.
- Introducir las tuercas en sus respectivos huecos del soporte de los sensores. Si no entran bien, ayudarse de un soldador para calentar lo suficiente las tuercas para que el plástico se pueda moldear. No calentar el exceso, o la pieza quedará deformada. También es muy importante que no se fuerce la tornillería y que las tuercas queden totalmente perpendiculares al tornillo para no estropear la rosca.
- Atornillar el soporte de los sensores al chasis
- Introducir los sensores encajándolos en sus respectivos huecos. Hay que tener cuidado para que no se queden mirando muy hacia arriba o hacia abajo. El GP2Y0A21 va en el frontal, ya que mide hasta 80 cm; mientras que los GP2Y0A41 van en los laterales, llegando a medir hasta 35 cm.

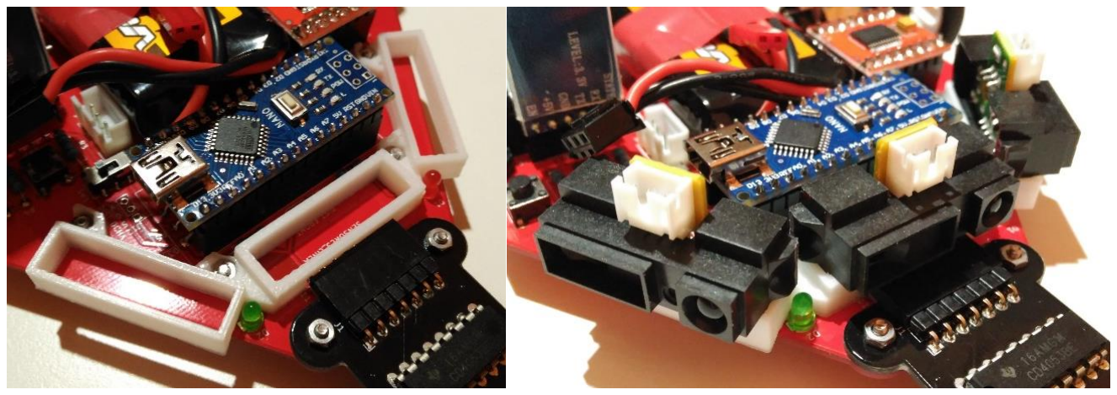
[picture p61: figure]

- Cortar los cables de los sensores, pelar los extremos y conectarlos a los sensores. Uno a uno, hay que ir soldando los cables de los sensores a sus respectivos pines en la PCB (conectores DSIT_FRONT, DIST_IZQ y DIST_DCHA), que pueden verse marcados en la serigrafía con V, G y S, siendo:
- Cable rojo = V
- Cable negro = G
- Cable amarillo = S

La serigrafía del sensor frontal no se ve porque el soporte de sensores la tapa. Para ver V, G y S, se puede acceder a los archivos de Kicad y ver el diseño de la placa o simplemente fijarse en que los cables van en orden, soldados en la PCB sin cruzarse, al igual que en los otros sensores.

Como extra, aunque en las primeras pruebas no ha resultado necesario, se puede añadir una visera a los sensores que apantalla la luz que pueda ser reflejada por el suelo. Así se evitan falsas detecciones si el sensor está apuntando demasiado bajo. Estas viseras van encajadas a presión sobre la parte frontal del sensor, como muestra la siguiente imagen.

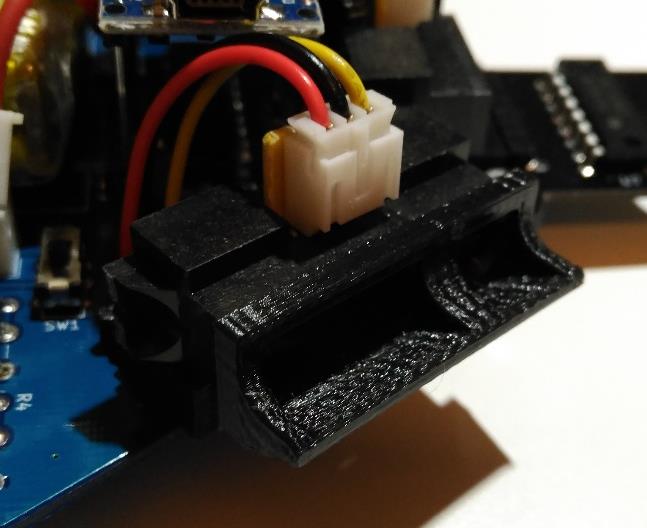
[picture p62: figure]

Pantalla trasera

La pantalla trasera es un extra que por normativa en la LNRC se tiene que poner en el robot. Además, tiene que ser blanca y de unas dimensiones adecuadas para que los demás robots puedan verlo.

Materiales necesarios:

- Pantalla
- 2x tuerca M2
- 2x tornillo M2x5mm

Para introducir las tuercas en los huecos de la pantalla, se necesitará calentarlas con un soldador, teniendo cuidado de no aplastarlas demasiado, lo cual haría que se cerrase el agujero al derretir el plástico en exceso.

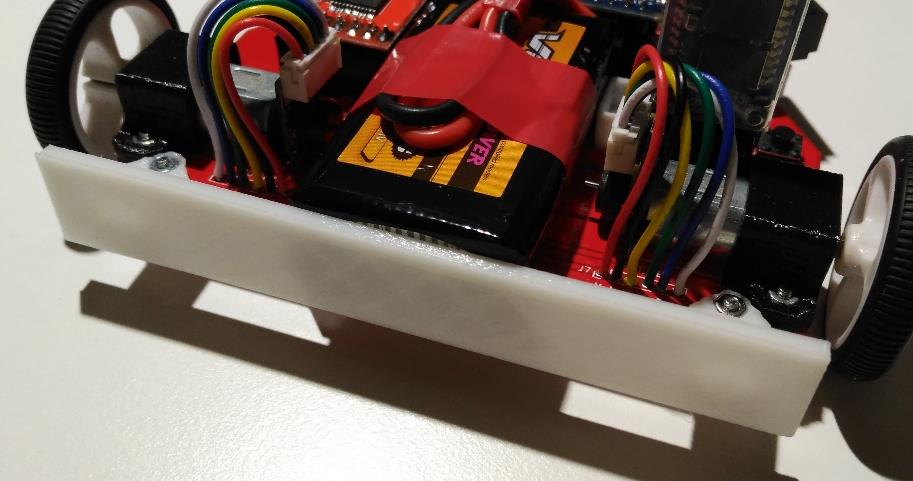
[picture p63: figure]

Cámara

Materiales necesarios:

- Cámara TSL1401
- Soporte de cámara
- Conector macho vertical de 5 pines
- 5 cables hembra-hembra de 10 cm
- 4x tuerca M2
- 4x tornillo M2x5mm
- 2x tuerca M3
- 2x tornillo M3

La cámara mostrada en la imagen anterior puede no ser exactamente igual a la del kit por la diferencia en la PCB sobre la que puede ir montada o los pines de conexión, pero sigue siendo una TSL1401, por lo que la programación será la misma. Más adelante se explica cómo conectar la cámara en función de los pines que tenga. Además, para cada uno de los dos modelos de cámara que se han probado, se ha diseñado un soporte diferente, ya que cada una de ellas se atornilla de manera distinta.

Los pasos para realizar el montaje de la cámara son los siguientes:

- Soldar el conector de 5 pines justo delante del motor izquierdo.
- Introducir las tuercas M2 en las ranuras del soporte de la cámara. Se necesitará calentarlas con el soldador. Al igual que en las piezas anteriores, hay que tener cuidado de no aplastarlas demasiado para no deformar la pieza y cerrar los agujeros.

- Utilizar los tornillos M2 para atornillar el soporte al chasis, con cuidado de que no se salgan las tuercas. Los mástiles más anchos del soporte van hacia la parte trasera, de tal manera que la cámara quedará un poco inclinada hacia delante para ver la línea a seguir.
- Utilizar los tornillos y tuercas M3 para atornillar la cámara al soporte. Dependiendo del modelo de cámara, se atornillará por delante o por detrás (la cámara de APTech por delante; la de Aliexpress, que tiene los pines acodados, por detrás).
- Conectar la cámara al conector de 5 pines mediante los cables hembra-hembra.
- Cámara APTech: como puede verse en las siguientes imágenes, los cables van conectados en el mismo orden en la cámara y el conector.

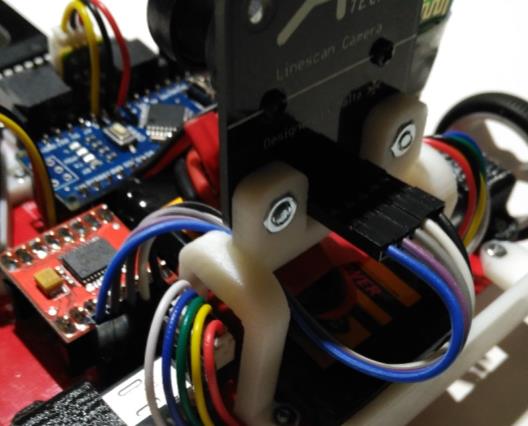
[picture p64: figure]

- Cámara de Aliexpress: en este caso, la cámara tiene 6 pines en dos filas acodadas (de ahí la razón por la que se atornilla por detrás y queda un poco más alta).

El pin adicional que presenta (AO0) es la salida original de los datos que recoge la cámara. Se puede utilizar ese pin o el de la salida filtrada (AO). En el caso de la cámara de APTech solamente se tiene el pin AO, que es la salida sin filtrar.

Para facilitar el cableado de esta cámara sin equivocarse en las conexiones, a continuación, se nombran los pines de ambas partes:

- Conector del chasis (de izquierda a derecha): GND, VCC, AO, CLK, SI
- Conector de la cámara:
- Fila delantera (de izquierda a derecha): VCC, AO0, GND
- Fila trasera (de izquierda a derecha): AO, CLK, SI

En las siguientes imágenes puede verse la relación de pines con los colores de cable que se han empleado: GND (marrón), VCC (rojo), AO (naranja), CLK (amarillo), SI (verde).

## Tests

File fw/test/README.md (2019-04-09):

Este programa de test sirve para probar cada una de las partes del robot:
- Pulsadores
- Leds
- Batería
- Sensores de línea
- Sensores de distancia
- Motores
- Encoders
- Cámara

Para que todo funcione correctamente debes haber seguido las indicaciones del [tutorial de primeras pruebas](https://github.com/Resaj/cyclops-project/blob/master/manuals/Tutorial%205%20-%20Primeras%20pruebas.pdf), donde aparecen las configuraciones necesarias para las diferentes partes del robot.

Para ello basta con descomentar las definiciones de los test correspondientes a los dispositivos que se quiere probar. Estos se encuentran al principio del programa:

```
//#define TEST_LEDS
//#define TEST_PULSADORES
//#define TEST_BATERIA
//#define TEST_SENSORES_LINEA
//#define TEST_SENSORES_DISTANCIA
//#define TEST_MOTORES
//#define TEST_ENCODERS
//#define TEST_CAMARA
```

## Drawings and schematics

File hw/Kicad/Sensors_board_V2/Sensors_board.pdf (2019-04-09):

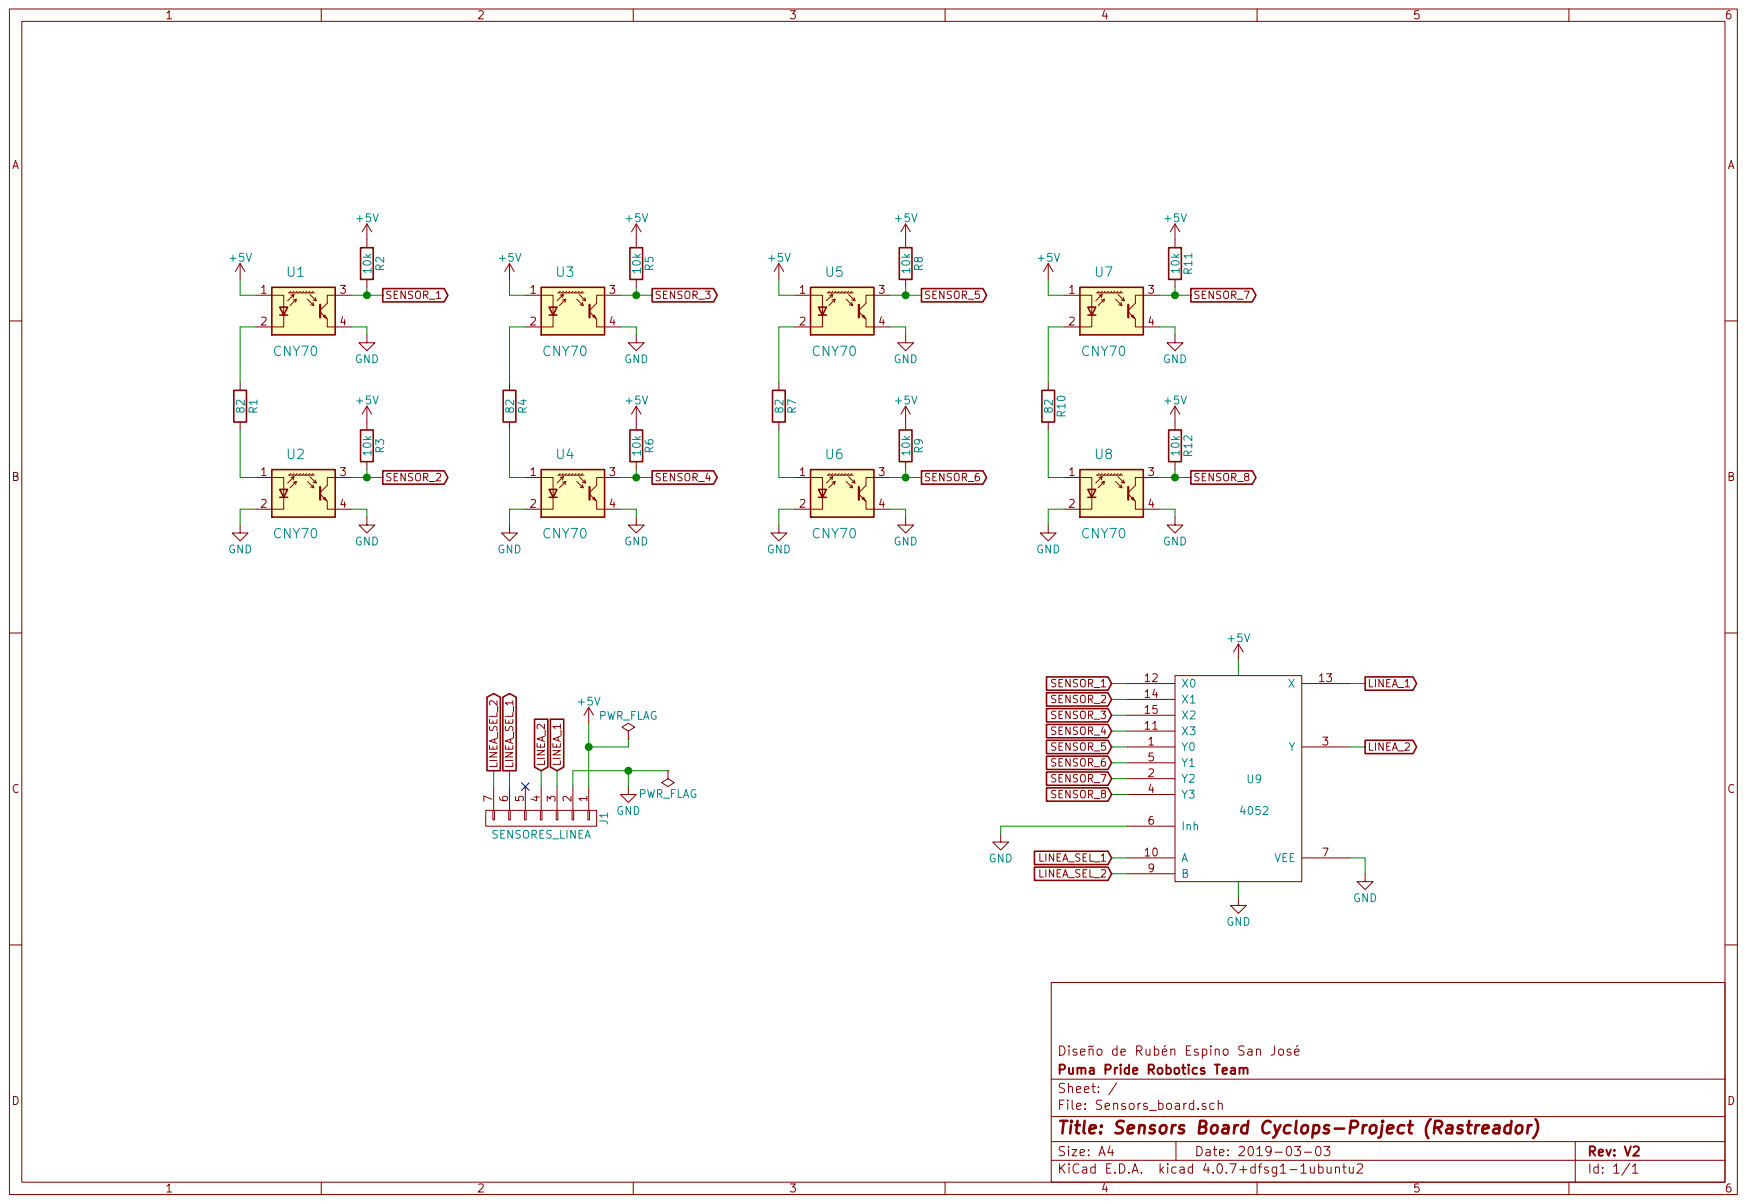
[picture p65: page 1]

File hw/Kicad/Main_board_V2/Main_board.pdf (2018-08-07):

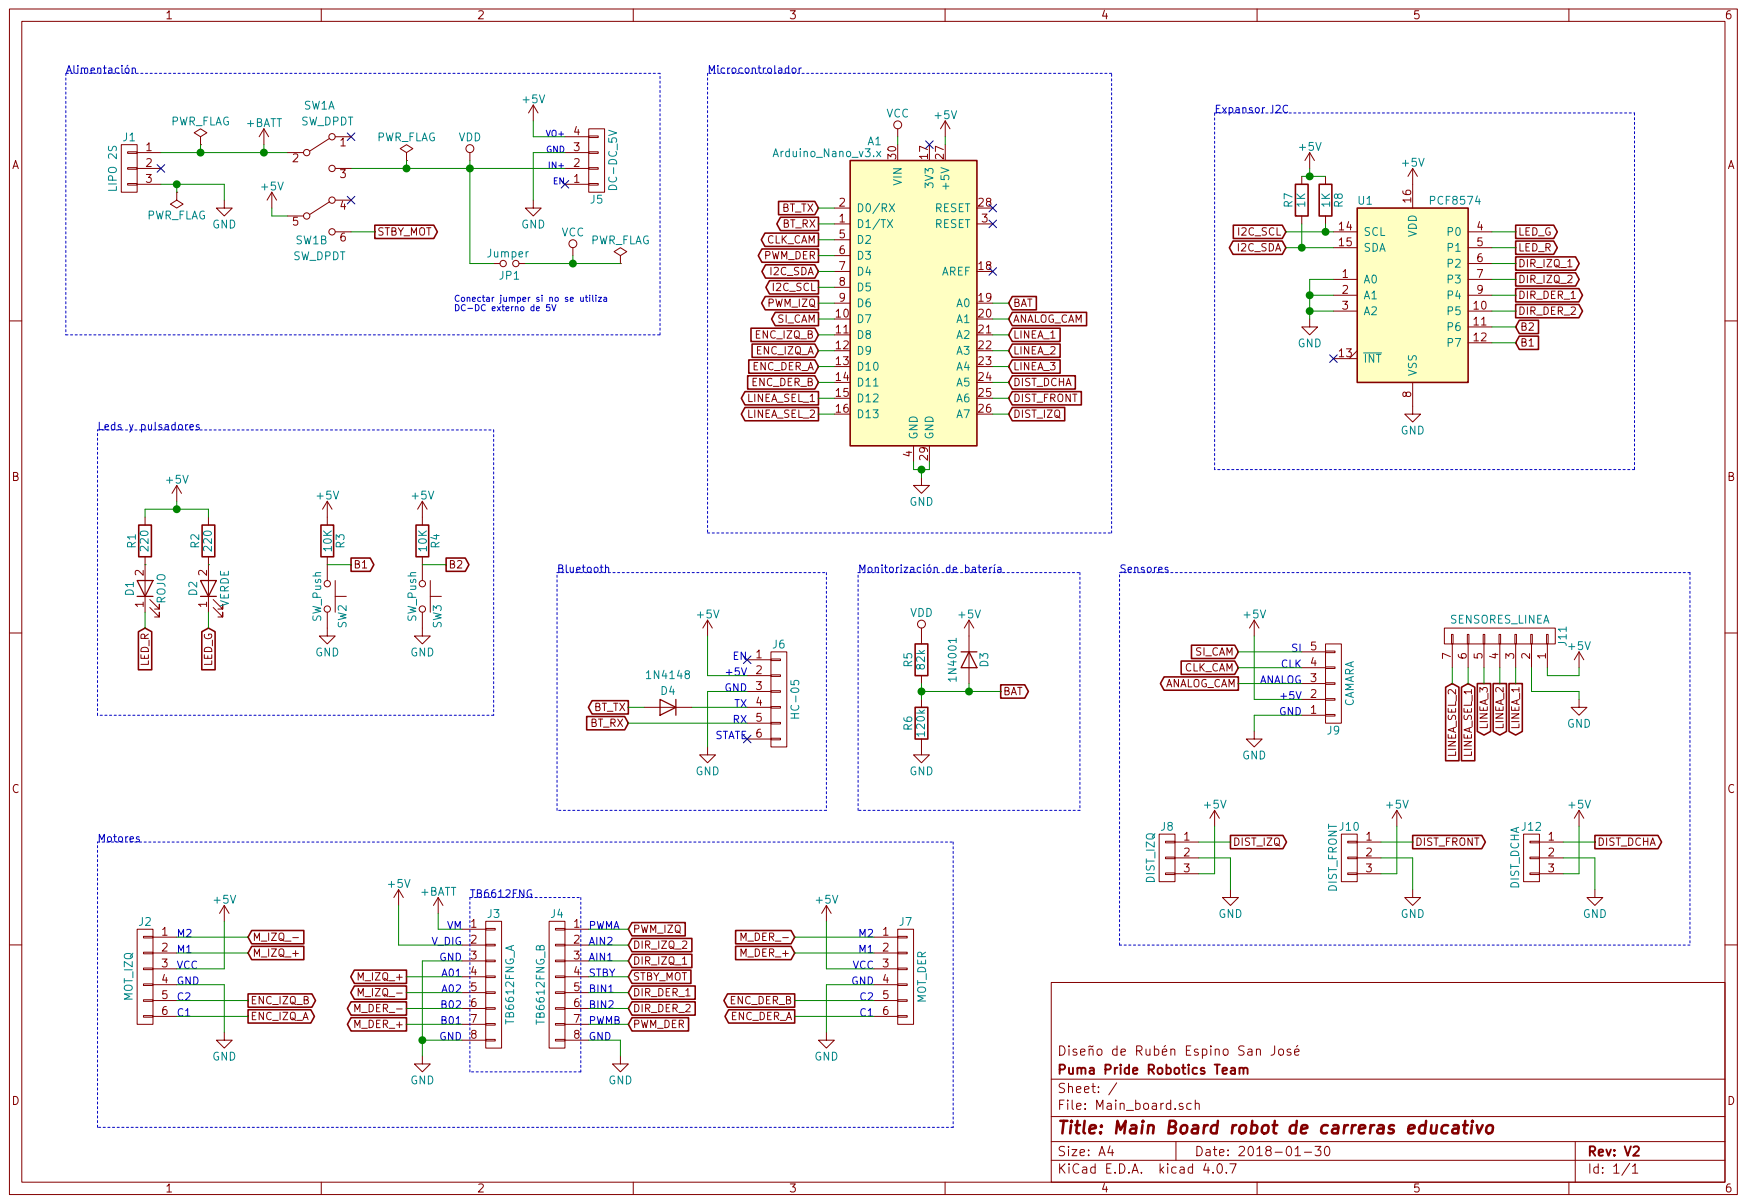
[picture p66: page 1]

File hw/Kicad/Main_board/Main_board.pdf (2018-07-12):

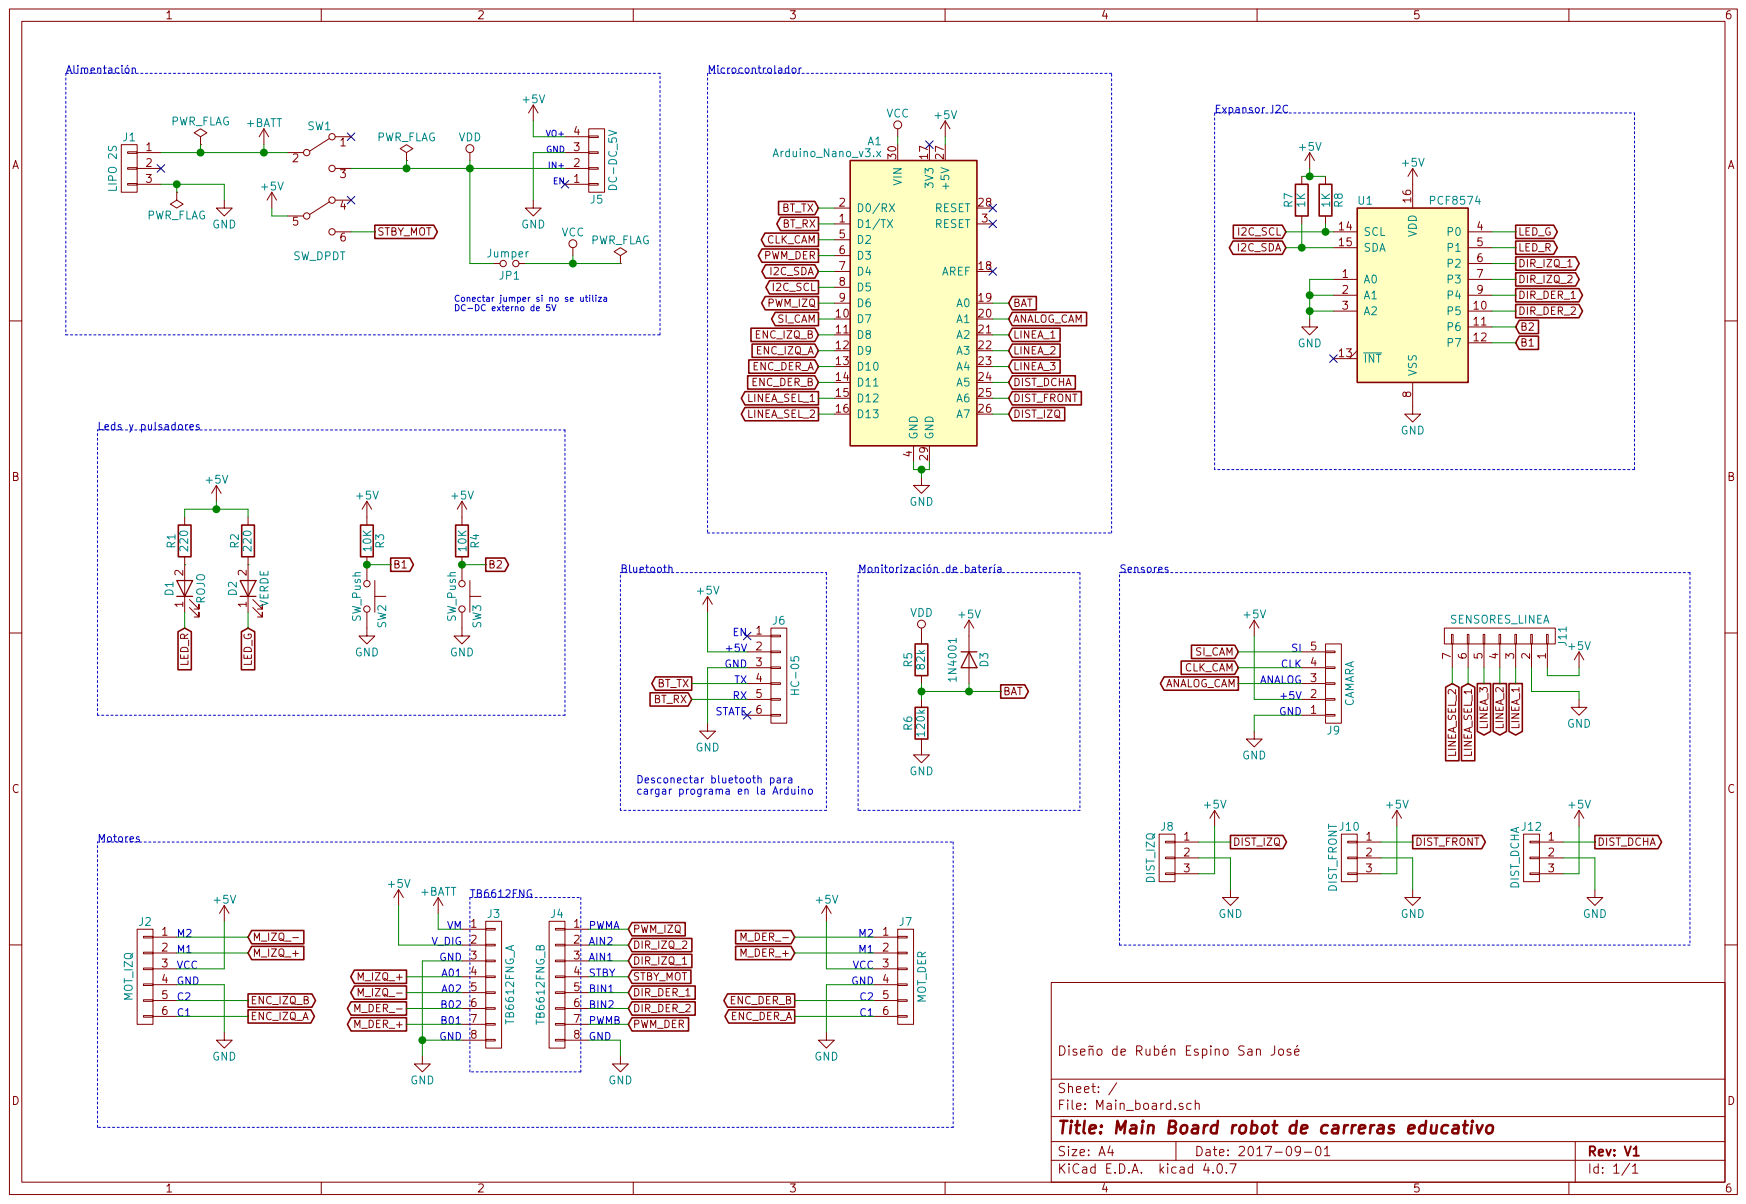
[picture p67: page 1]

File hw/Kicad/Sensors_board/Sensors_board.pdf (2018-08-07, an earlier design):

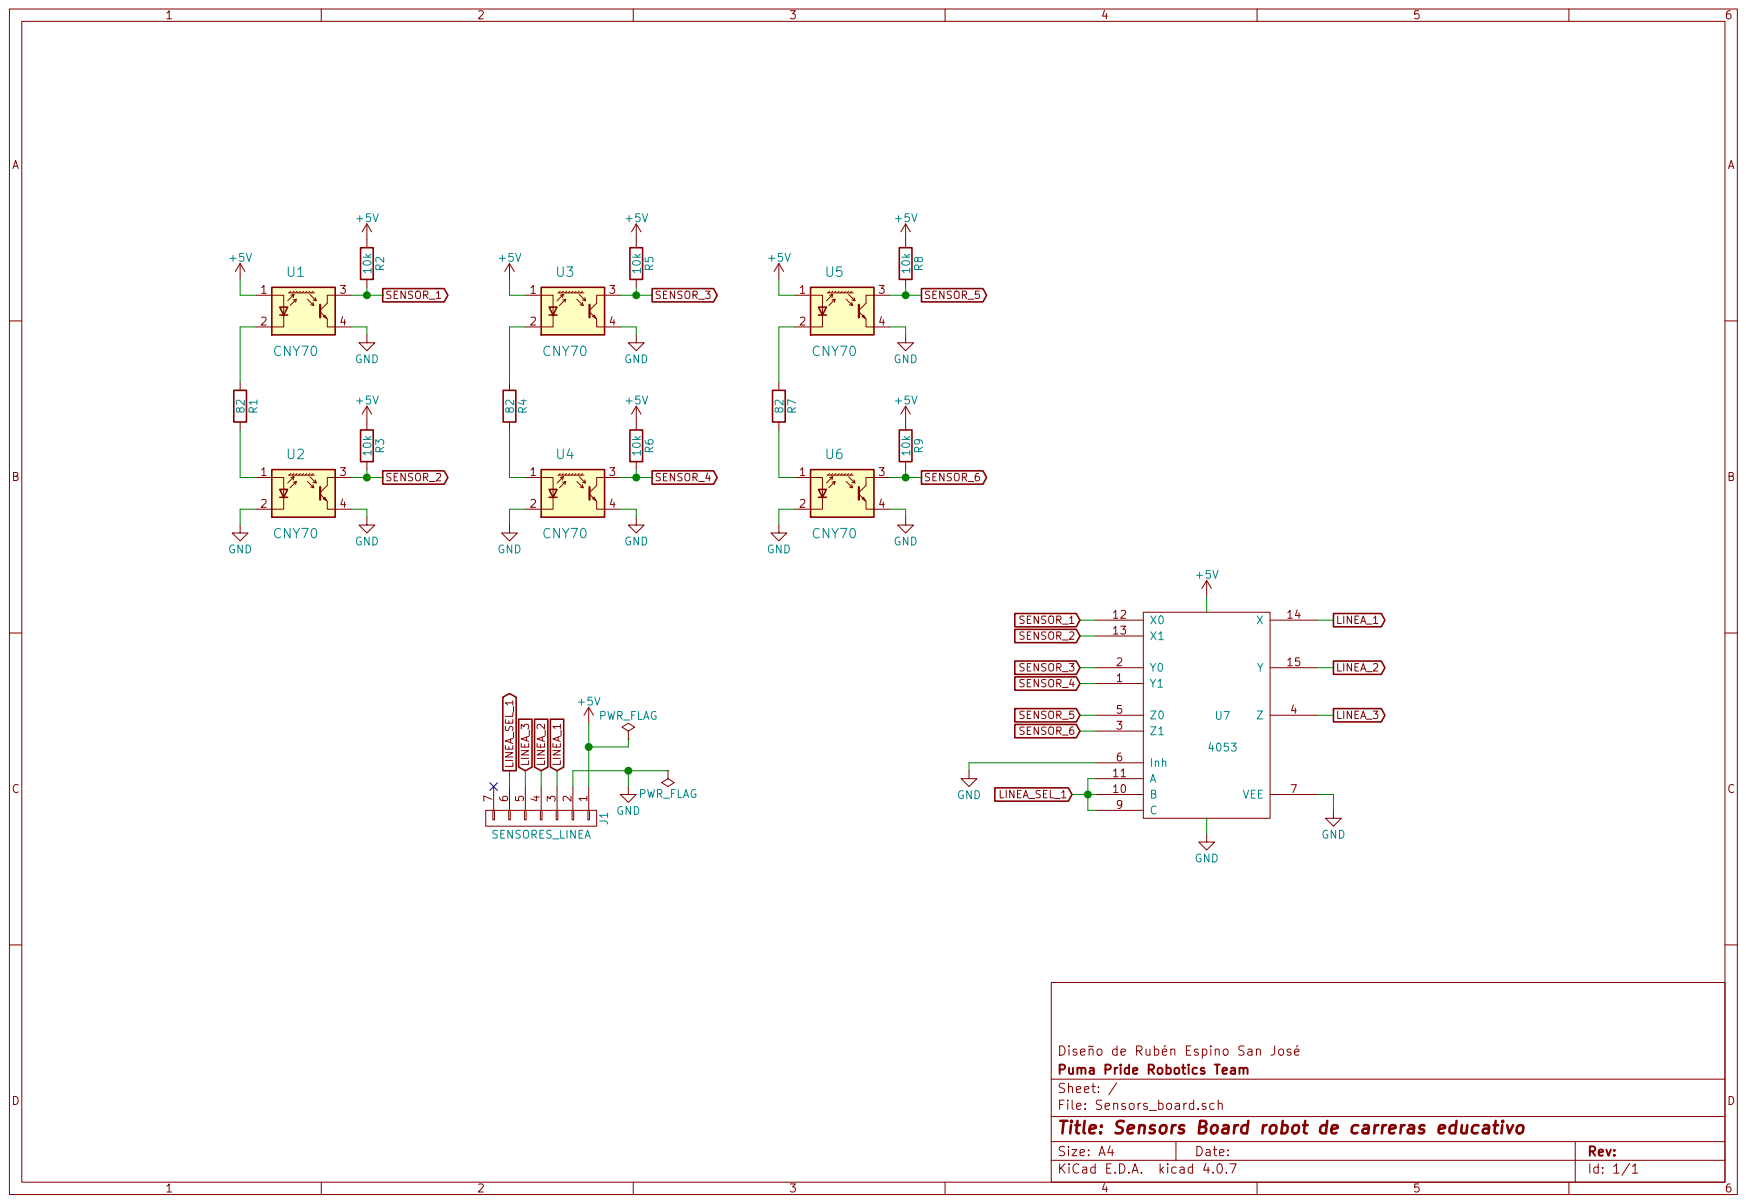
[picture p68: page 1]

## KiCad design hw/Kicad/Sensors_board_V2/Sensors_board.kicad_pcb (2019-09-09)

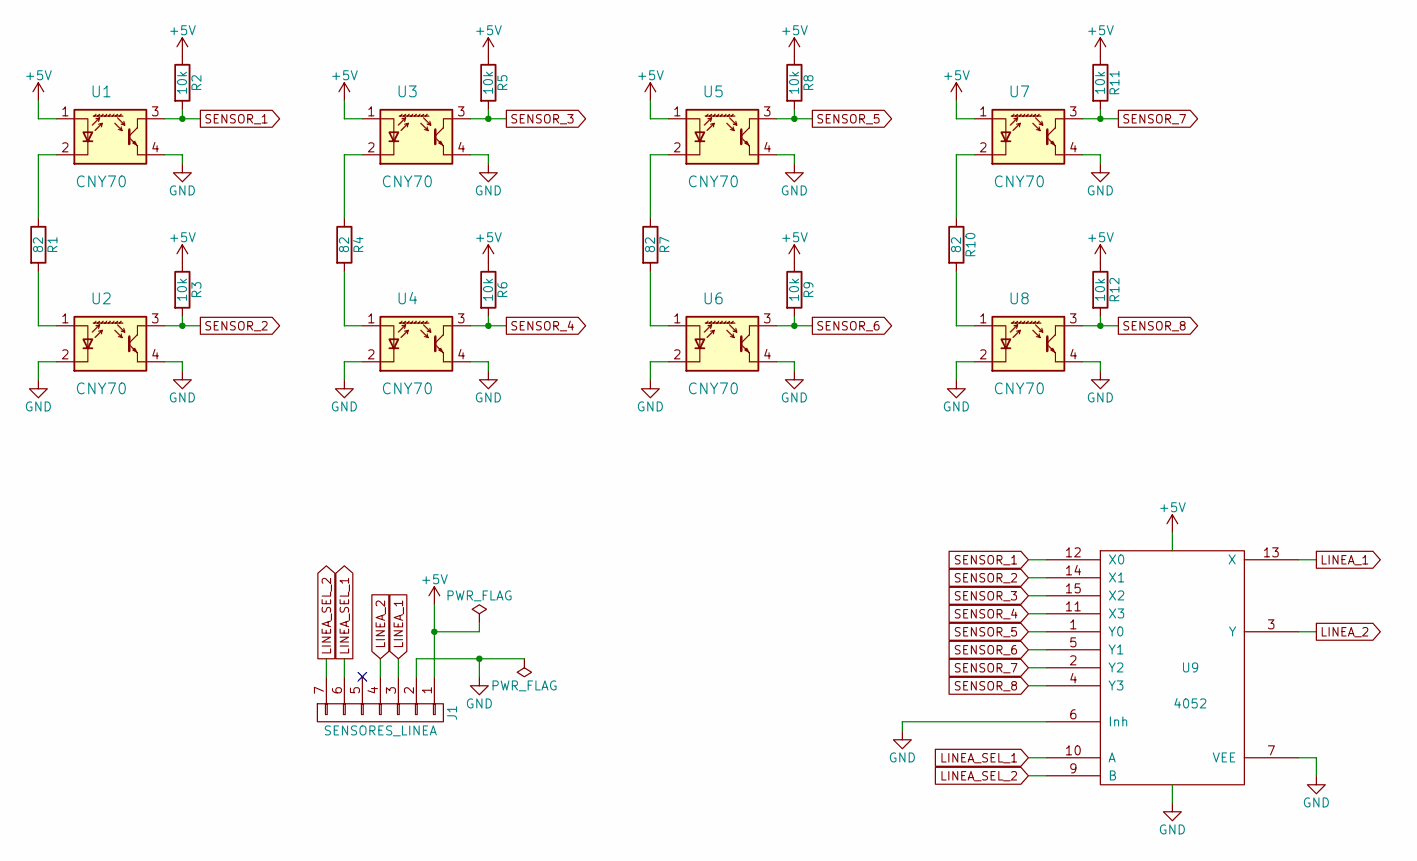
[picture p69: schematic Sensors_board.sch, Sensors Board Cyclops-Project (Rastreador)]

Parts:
J1: SENSORES_LINEA; PinHeader_1x07_P2.54mm_Horizontal
R1, R4, R7, R10: 82; R_Axial_DIN0207_L6.3mm_D2.5mm_P10.16mm_Horizontal
R2, R3, R5, R6, R8, R9, R11, R12: 10k; R_Axial_DIN0207_L6.3mm_D2.5mm_P10.16mm_Horizontal
U1, U2, U3, U4, U5, U6, U7, U8: CNY70; Vishay_CNY70
U9: 4052; DIP-16_W7.62mm_Socket_LongPads

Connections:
+5V: J1.1, R2.1, R3.1, R5.1, R6.1, R8.1, R9.1, R11.1, R12.1, U1.1 (A), U3.1 (A), U5.1 (A), U7.1 (A), U9.16 (VDD)
GND: J1.2, U1.4 (E), U2.2 (K), U2.4 (E), U3.4 (E), U4.2 (K), U4.4 (E), U5.4 (E), U6.2 (K), U6.4 (E), U7.4 (E), U8.2 (K), U8.4 (E), U9.6 (Inh), U9.7 (VEE), U9.8 (VSS)
LINEA_1: J1.3, U9.13 (X)
LINEA_2: J1.4, U9.3 (Y)
LINEA_SEL_1: J1.6, U9.10 (A)
LINEA_SEL_2: J1.7, U9.9 (B)
unnamed: R1.1, U1.2 (K)
unnamed: R1.2, U2.1 (A)
unnamed: R4.1, U3.2 (K)
unnamed: R4.2, U4.1 (A)
unnamed: R7.1, U5.2 (K)
unnamed: R7.2, U6.1 (A)
unnamed: R10.1, U7.2 (K)
unnamed: R10.2, U8.1 (A)
SENSOR_1: R2.2, U1.3 (C), U9.12 (X0)
SENSOR_2: R3.2, U2.3 (C), U9.14 (X1)
SENSOR_3: R5.2, U3.3 (C), U9.15 (X2)
SENSOR_4: R6.2, U4.3 (C), U9.11 (X3)
SENSOR_5: R8.2, U5.3 (C), U9.1 (Y0)
SENSOR_6: R9.2, U6.3 (C), U9.5 (Y1)
SENSOR_7: R11.2, U7.3 (C), U9.2 (Y2)
SENSOR_8: R12.2, U8.3 (C), U9.4 (Y3)

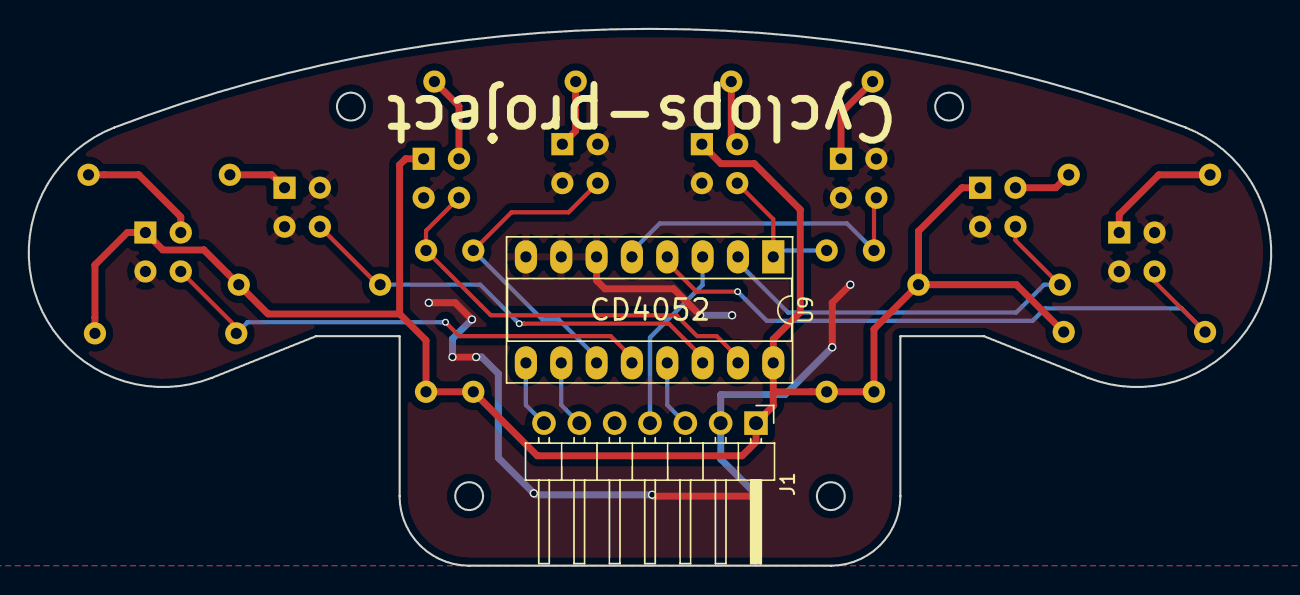
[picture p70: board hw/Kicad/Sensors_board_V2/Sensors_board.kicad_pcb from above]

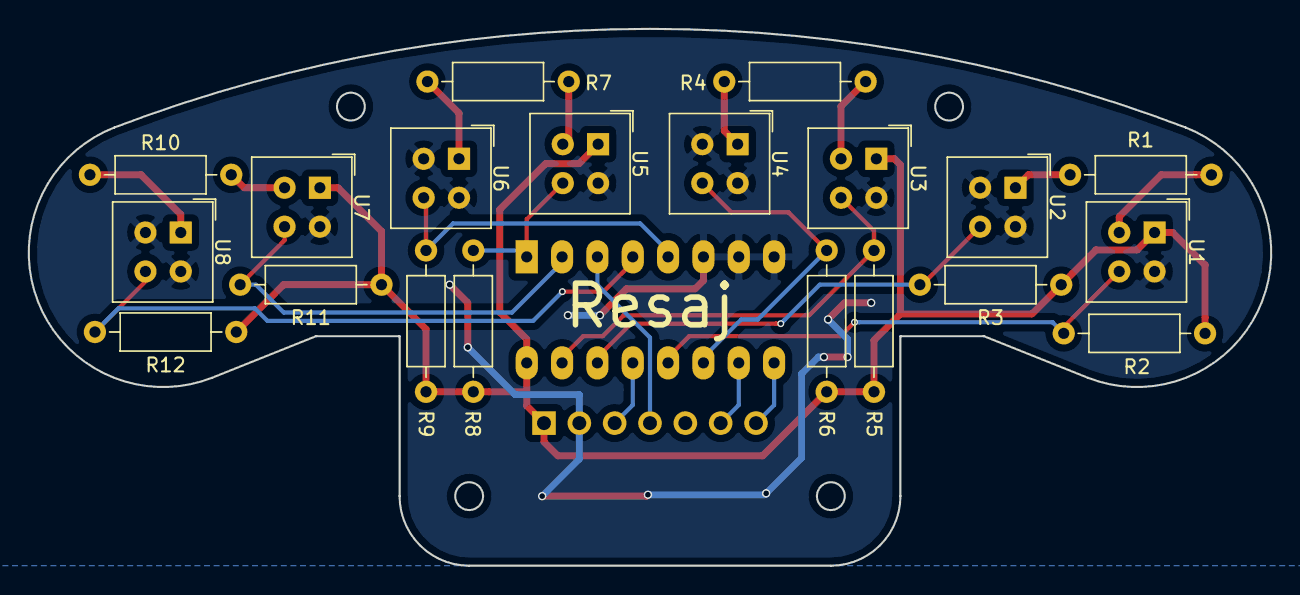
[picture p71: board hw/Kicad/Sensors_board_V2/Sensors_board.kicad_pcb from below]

Board: 2 copper layers, 89.3 x 38.6 mm, 22 parts (20 on the bottom side), 22 nets.

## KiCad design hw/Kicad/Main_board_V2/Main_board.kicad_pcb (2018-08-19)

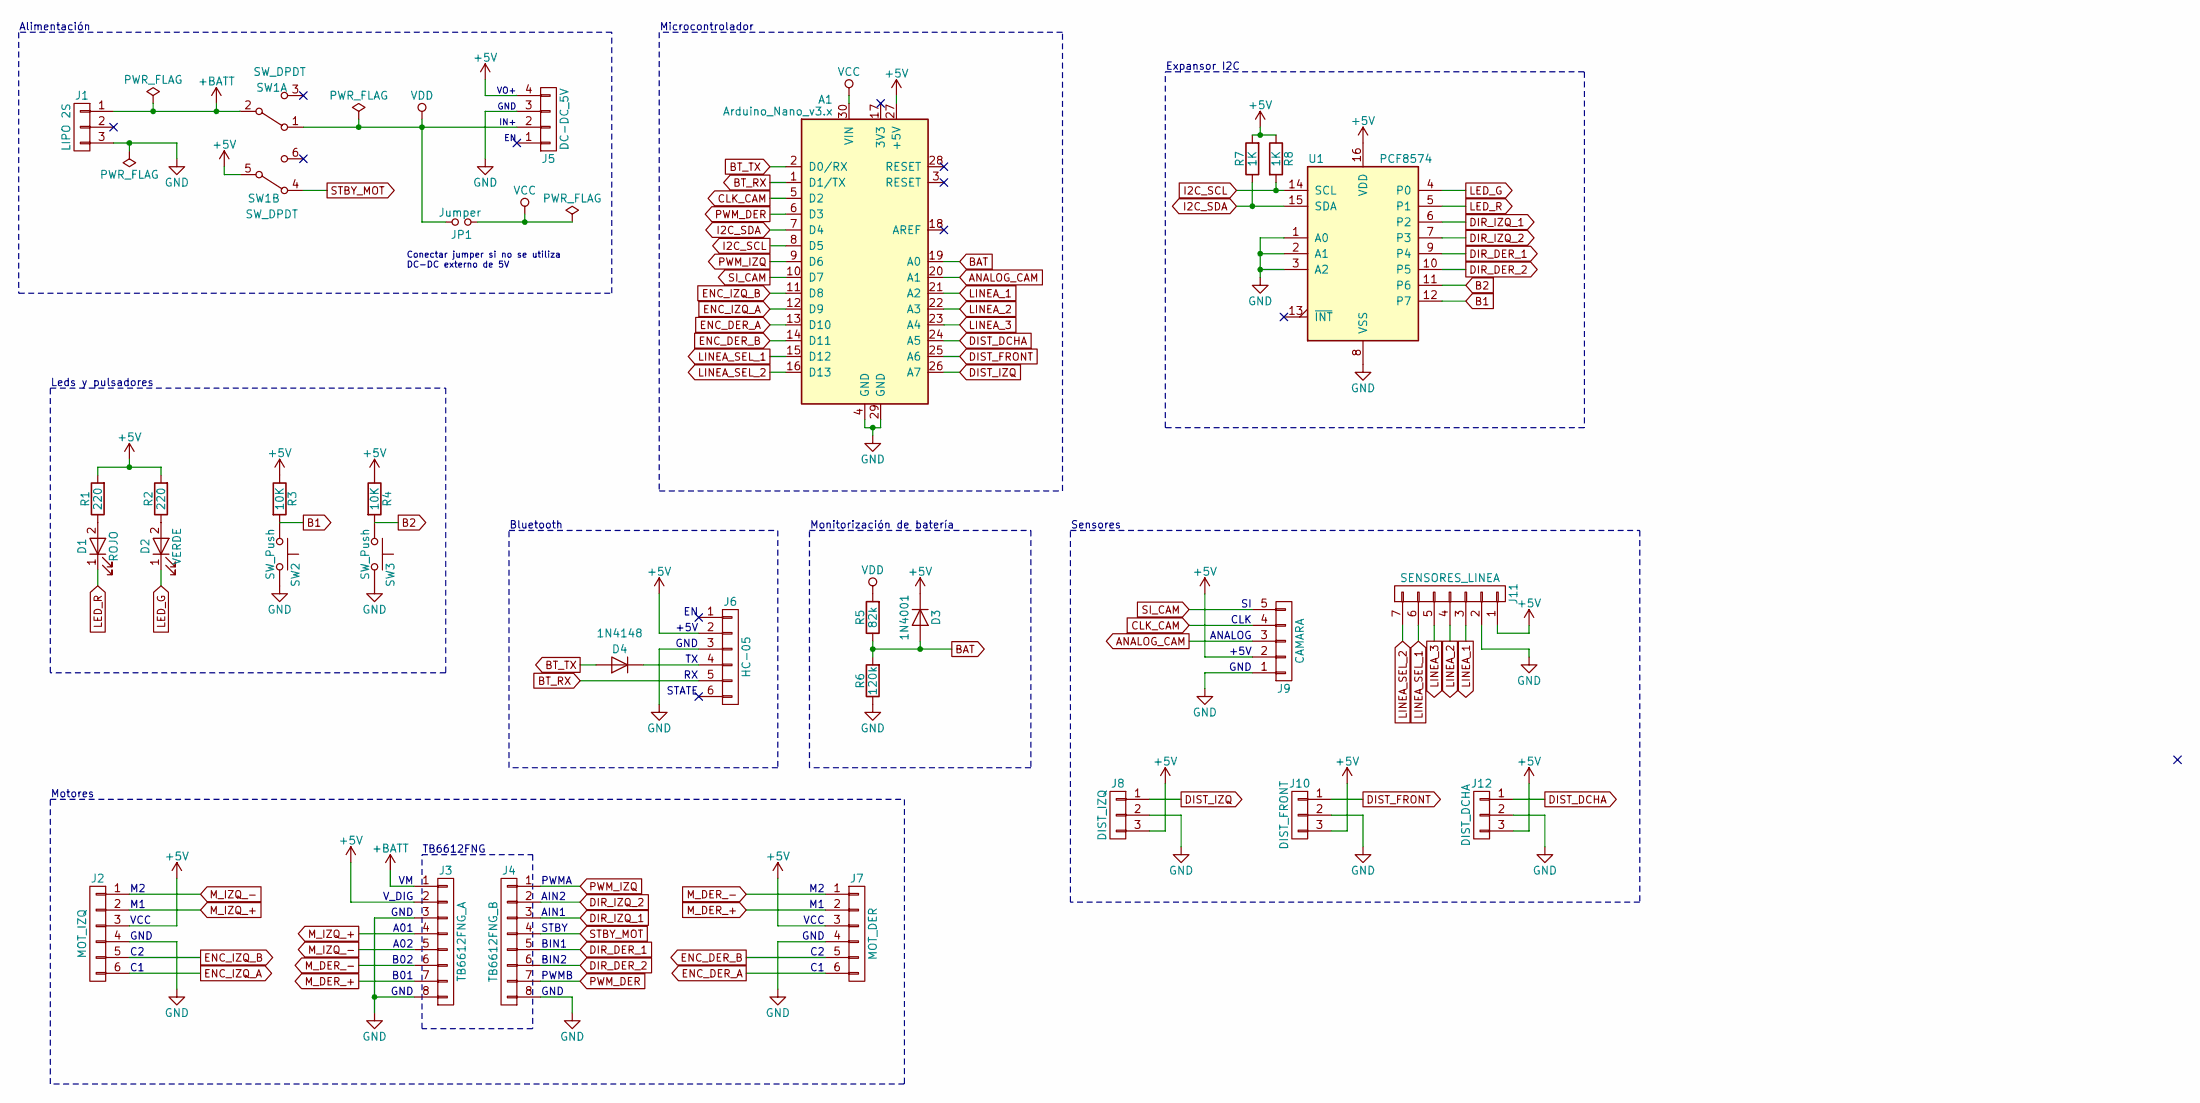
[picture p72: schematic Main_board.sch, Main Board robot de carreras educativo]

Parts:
A1: Arduino_Nano_v3.x; Arduino_Nano
D1: ROJO; LED_D3.0mm
D2: VERDE; LED_D3.0mm
D3: 1N4001; D_A-405_P10.16mm_Horizontal
D4: 1N4148; D_A-405_P10.16mm_Horizontal
J1: LIPO 2S; JST_XH_B03B-XH-A_1x03_P2.50mm_Vertical
J2: MOT_IZQ; PinHeader_1x06_P2.00mm_Vertical
J3: TB6612FNG_A; PinSocket_1x08_P2.54mm_Vertical
J4: TB6612FNG_B; PinSocket_1x08_P2.54mm_Vertical
J5: DC-DC_5V; PinSocket_1x04_P2.54mm_Horizontal
J6: HC-05; PinSocket_1x06_P2.54mm_Vertical
J7: MOT_DER; PinHeader_1x06_P2.00mm_Vertical
J8: DIST_IZQ; PinHeader_1x03_P2.00mm_Vertical
J9: CAMARA; PinHeader_1x05_P2.54mm_Vertical
J10: DIST_FRONT; PinHeader_1x03_P2.00mm_Vertical
J11: SENSORES_LINEA; PinSocket_1x07_P2.54mm_Horizontal
J12: DIST_DCHA; PinHeader_1x03_P2.00mm_Vertical
JP1: Jumper; SolderJumper-2_P1.3mm_Open_Pad1.0x1.5mm
R1, R2: 220; R_Axial_DIN0207_L6.3mm_D2.5mm_P10.16mm_Horizontal
R3, R4: 10K; R_Axial_DIN0207_L6.3mm_D2.5mm_P10.16mm_Horizontal
R5: 82k; R_Axial_DIN0207_L6.3mm_D2.5mm_P10.16mm_Horizontal
R6: 120k; R_Axial_DIN0207_L6.3mm_D2.5mm_P10.16mm_Horizontal
R7, R8: 1K; R_Axial_DIN0207_L6.3mm_D2.5mm_P10.16mm_Horizontal
SW1: SW_DPDT; SW_CuK_JS202011CQN_DPDT_Straight
SW2, SW3: SW_Push; SW_PUSH_6mm
U1: PCF8574; DIP-16_W7.62mm_Socket_LongPads

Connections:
+5V: A1.27 (+5V), D3.1 (K), J2.3, J3.2, J5.4, J6.2, J7.3, J8.3, J9.2, J10.3, J11.1, J12.3, R1.2, R2.2, R3.1, R4.1, R7.2, R8.1, SW1.5 (B), U1.16 (VDD)
+BATT: J1.1, J3.1, SW1.2 (B)
ANALOG_CAM: A1.20 (A1), J9.3
B1: R3.2, SW2.1, U1.12 (P7)
B2: R4.2, SW3.1, U1.11 (P6)
BAT: A1.19 (A0), D3.2 (A), R5.1, R6.2
BT_RX: A1.1 (D1/TX), J6.5
BT_TX: A1.2 (D0/RX), D4.2 (A)
CLK_CAM: A1.5 (D2), J9.4
DIR_DER_1: J4.5, U1.9 (P4)
DIR_DER_2: J4.6, U1.10 (P5)
DIR_IZQ_1: J4.3, U1.6 (P2)
DIR_IZQ_2: J4.2, U1.7 (P3)
DIST_DCHA: A1.24 (A5), J12.1
DIST_FRONT: A1.25 (A6), J10.1
DIST_IZQ: A1.26 (A7), J8.1
ENC_DER_A: A1.13 (D10), J7.6
ENC_DER_B: A1.14 (D11), J7.5
ENC_IZQ_A: A1.12 (D9), J2.6
ENC_IZQ_B: A1.11 (D8), J2.5
GND: A1.4 (GND), A1.29 (GND), J1.3, J2.4, J3.3, J3.8, J4.8, J5.3, J6.3, J7.4, J8.2, J9.1, J10.2, J11.2, J12.2, R6.1, SW2.2, SW3.2, U1.1 (A0), U1.2 (A1), U1.3 (A2), U1.8 (VSS)
I2C_SCL: A1.8 (D5), R8.2, U1.14 (SCL)
I2C_SDA: A1.7 (D4), R7.1, U1.15 (SDA)
LED_G: D2.1 (K), U1.4 (P0)
LED_R: D1.1 (K), U1.5 (P1)
LINEA_1: A1.21 (A2), J11.3
LINEA_2: A1.22 (A3), J11.4
LINEA_3: A1.23 (A4), J11.5
LINEA_SEL_1: A1.15 (D12), J11.6
LINEA_SEL_2: A1.16 (D13), J11.7
M_DER_+: J3.7, J7.2
M_DER_-: J3.6, J7.1
M_IZQ_+: J2.2, J3.4
M_IZQ_-: J2.1, J3.5
unnamed: D1.2 (A), R1.1
unnamed: D2.2 (A), R2.1
unnamed: D4.1 (K), J6.4
PWM_DER: A1.6 (D3), J4.7
PWM_IZQ: A1.9 (D6), J4.1
SI_CAM: A1.10 (D7), J9.5
STBY_MOT: J4.4, SW1.4 (A)
VCC: A1.30 (VIN), JP1.1
VDD: J5.2, JP1.2, R5.2, SW1.1 (A)

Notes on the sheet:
VO+
IN+
GND
Conectar jumper si no se utiliza DC-DC externo de 5V
Alimentación
Microcontrolador
Leds y pulsadores
Monitorización de batería
V_DIG
A01
A02
B02
B01
PWMB
PWMA
AIN2
AIN1
STBY
BIN1
BIN2
VCC
TB6612FNG
Motores
+5V
STATE
Bluetooth
ANALOG
CLK
Sensores
Expansor I2C

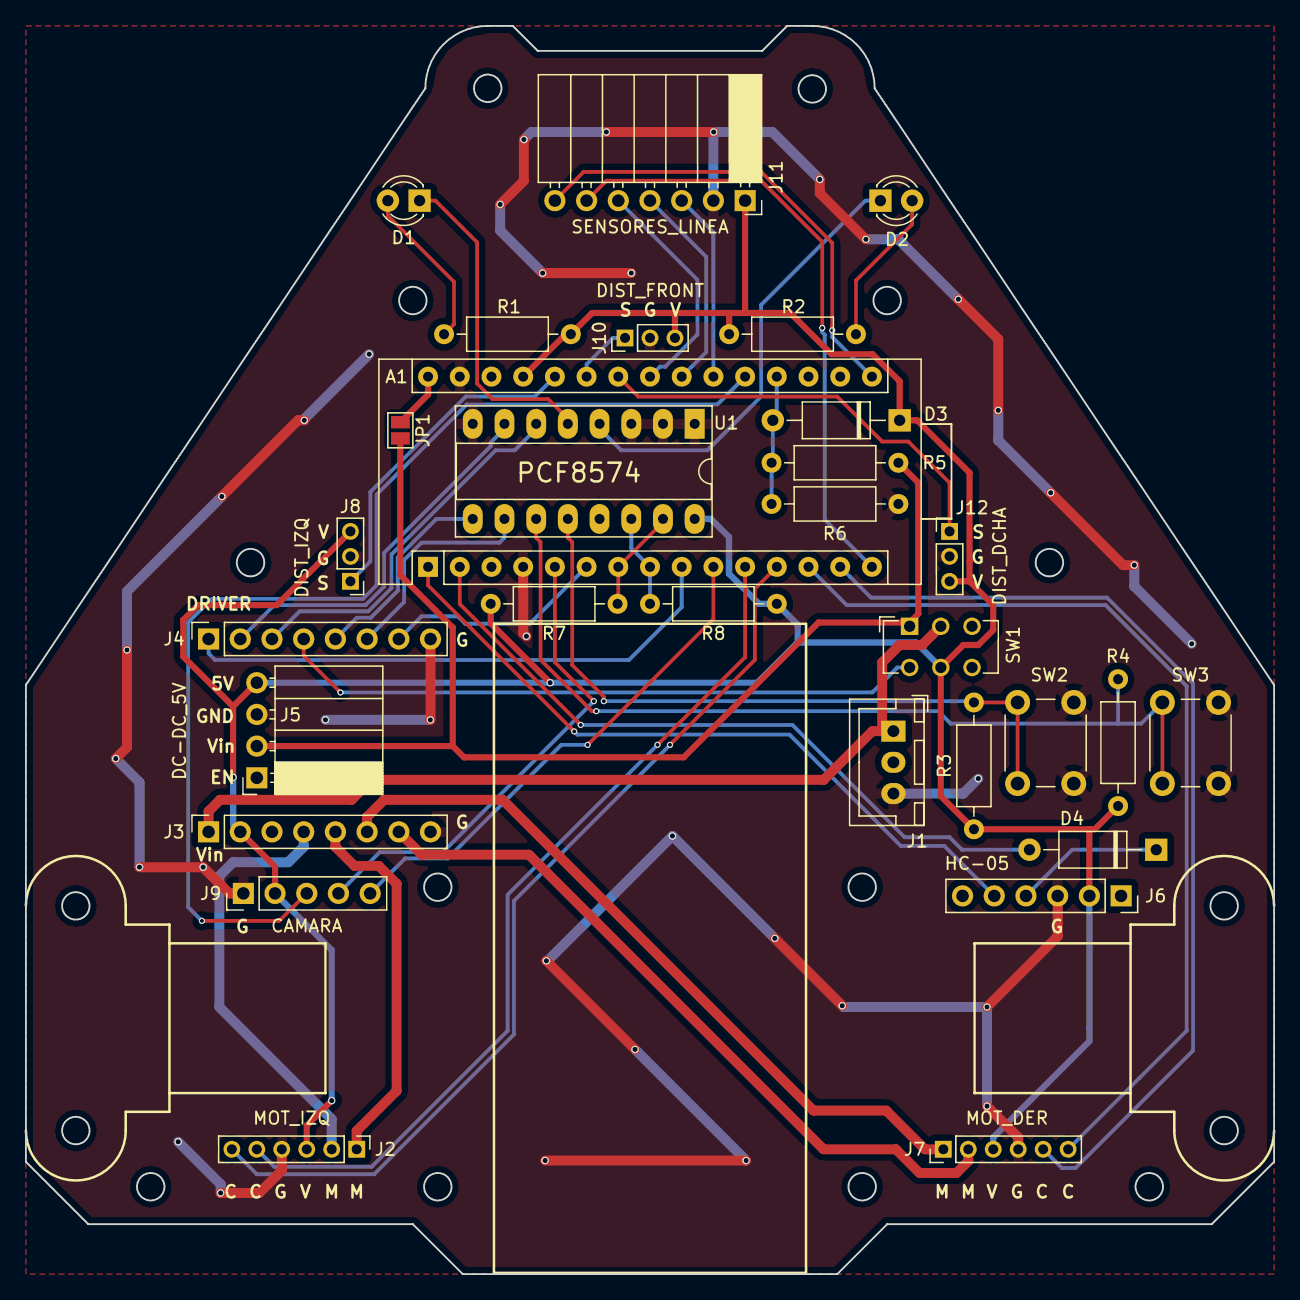
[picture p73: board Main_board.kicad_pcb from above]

Board: 2 copper layers, 100.0 x 100.0 mm, 30 parts (0 on the bottom side), 43 nets.

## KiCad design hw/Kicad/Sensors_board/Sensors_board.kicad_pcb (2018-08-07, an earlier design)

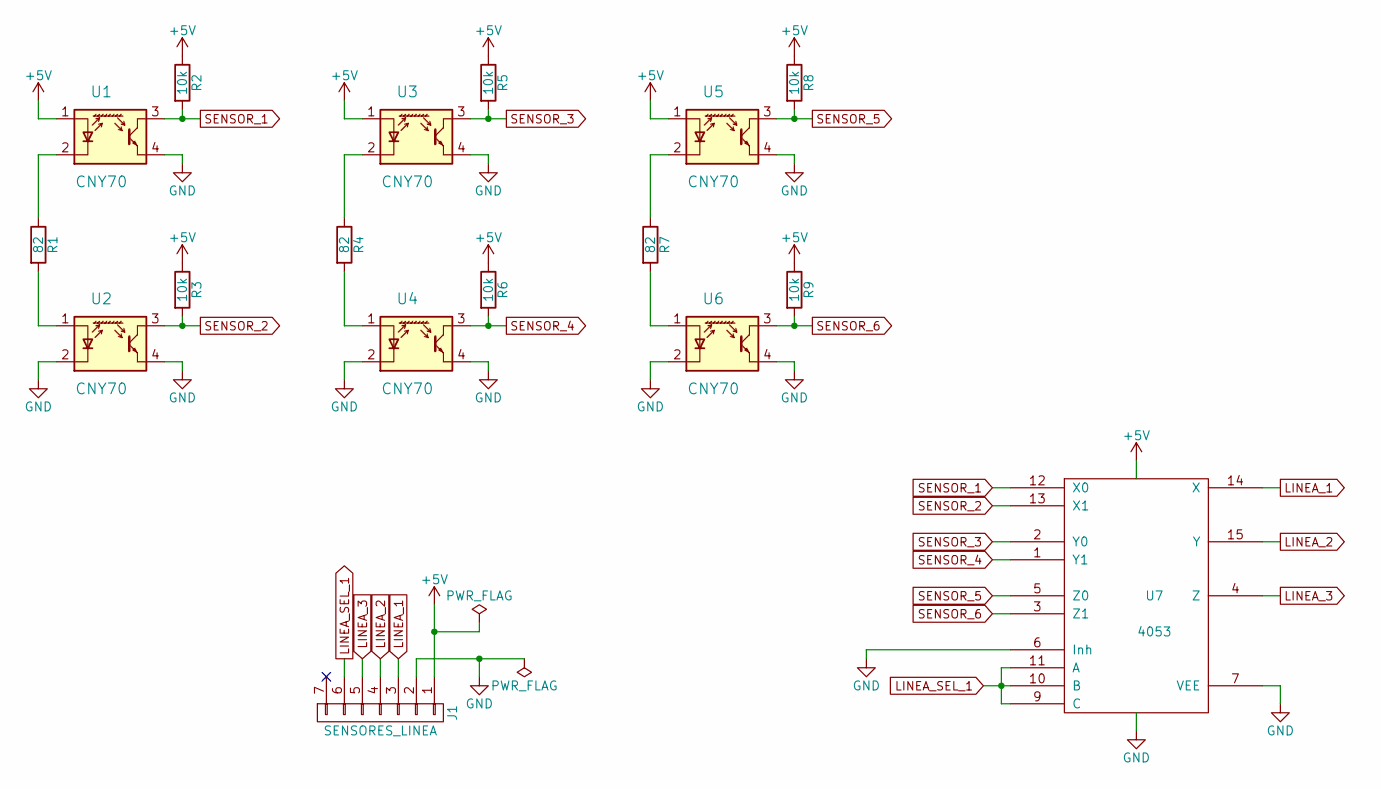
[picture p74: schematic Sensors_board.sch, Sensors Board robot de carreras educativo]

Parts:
J1: SENSORES_LINEA; PinHeader_1x07_P2.54mm_Horizontal
R1, R4, R7: 82; R_Axial_DIN0207_L6.3mm_D2.5mm_P10.16mm_Horizontal
R2, R3, R5, R6, R8, R9: 10k; R_Axial_DIN0207_L6.3mm_D2.5mm_P10.16mm_Horizontal
U1, U2, U3, U4, U5, U6: CNY70; Vishay_CNY70
U7: 4053; DIP-16_W7.62mm_Socket_LongPads

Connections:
+5V: J1.1, R2.1, R3.1, R5.1, R6.1, R8.1, R9.1, U1.1 (A), U3.1 (A), U5.1 (A), U7.16 (VDD)
GND: J1.2, U1.4 (E), U2.2 (K), U2.4 (E), U3.4 (E), U4.2 (K), U4.4 (E), U5.4 (E), U6.2 (K), U6.4 (E), U7.6 (Inh), U7.7 (VEE), U7.8 (VSS)
LINEA_1: J1.3, U7.14 (X)
LINEA_2: J1.4, U7.15 (Y)
LINEA_3: J1.5, U7.4 (Z)
LINEA_SEL_1: J1.6, U7.9 (C), U7.10 (B), U7.11 (A)
unnamed: R1.1, U1.2 (K)
unnamed: R1.2, U2.1 (A)
unnamed: R4.1, U3.2 (K)
unnamed: R4.2, U4.1 (A)
unnamed: R7.1, U5.2 (K)
unnamed: R7.2, U6.1 (A)
SENSOR_1: R2.2, U1.3 (C), U7.12 (X0)
SENSOR_2: R3.2, U2.3 (C), U7.13 (X1)
SENSOR_3: R5.2, U3.3 (C), U7.2 (Y0)
SENSOR_4: R6.2, U4.3 (C), U7.1 (Y1)
SENSOR_5: R8.2, U5.3 (C), U7.5 (Z0)
SENSOR_6: R9.2, U6.3 (C), U7.3 (Z1)

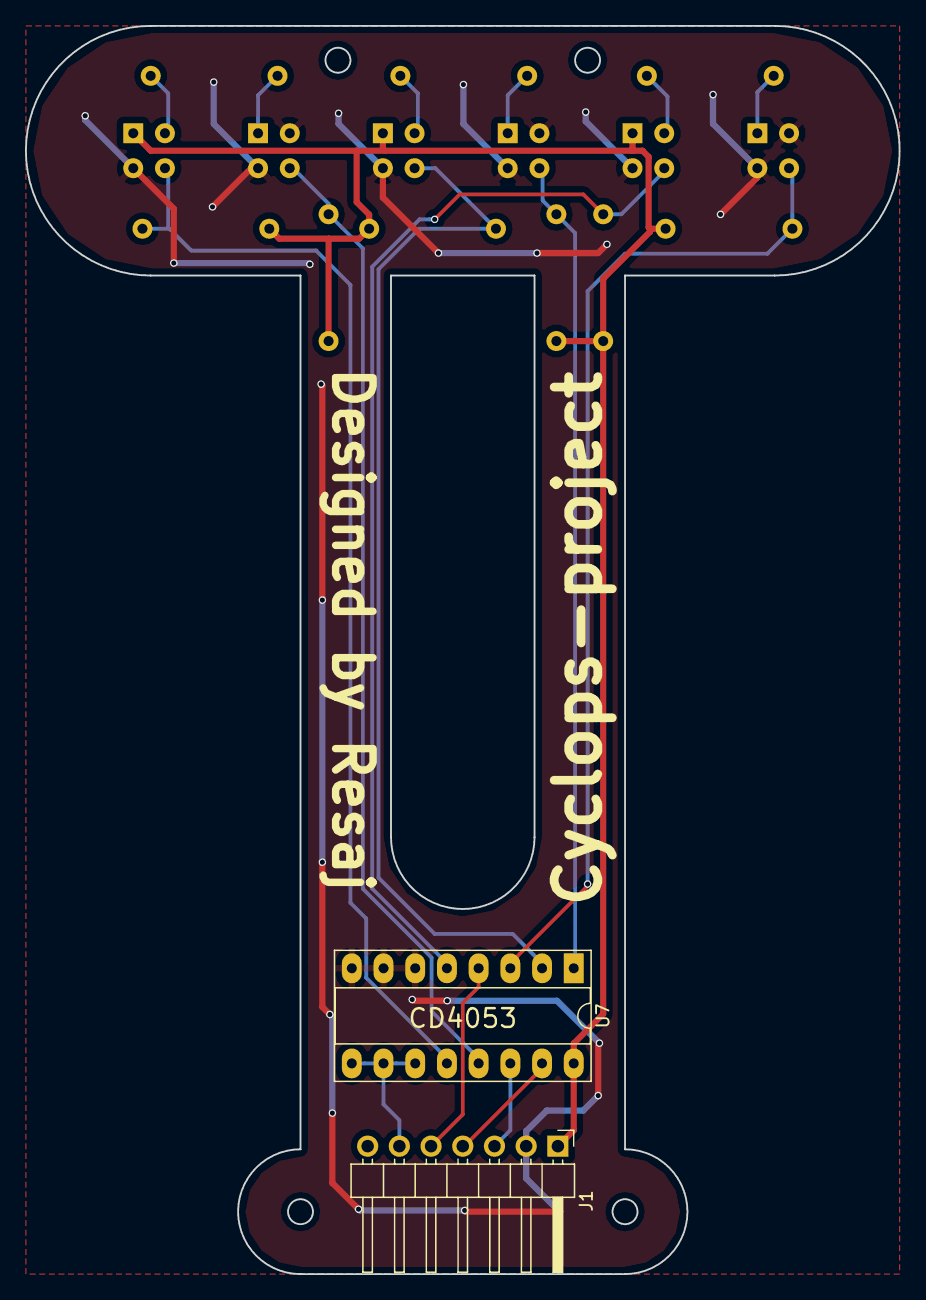
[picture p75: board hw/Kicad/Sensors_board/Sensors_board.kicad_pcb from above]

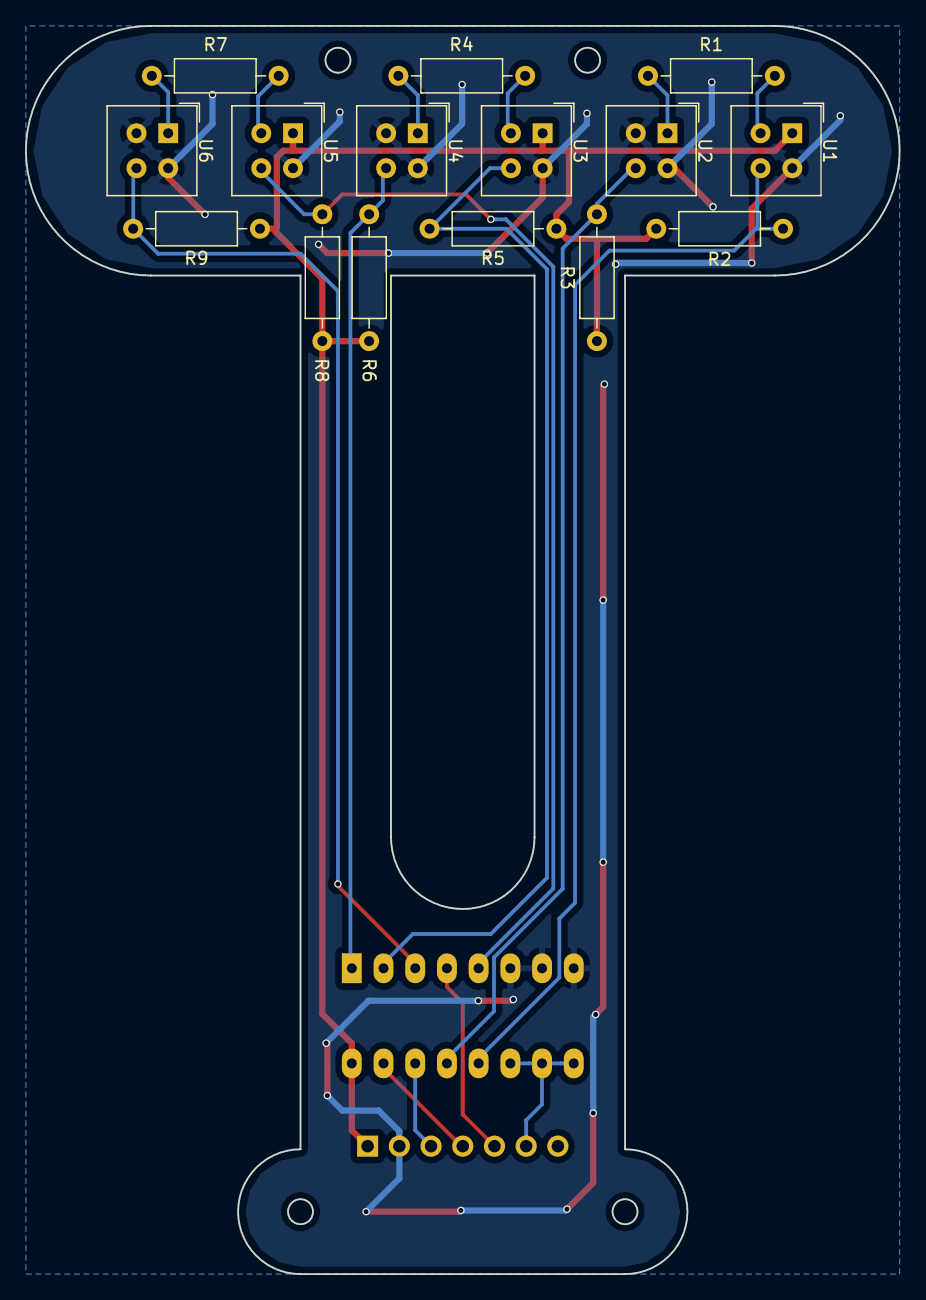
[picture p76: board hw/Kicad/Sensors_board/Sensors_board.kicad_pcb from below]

Board: 2 copper layers, 70.0 x 100.0 mm, 17 parts (15 on the bottom side), 18 nets.

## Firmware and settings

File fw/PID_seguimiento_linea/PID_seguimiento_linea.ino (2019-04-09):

//#define SEGUIMIENTO_CON_CAMARA

//EXPANSOR I2C PCF8574
#define SDA_PORT PORTD
#define SDA_PIN 4
#define SCL_PORT PORTD
#define SCL_PIN 5
#include <SoftWire.h>
SoftWire EXP = SoftWire();
const int expAddress = 0x20;
unsigned char expOutputRegister = 0b11111111;
void set_exp_value(char pin, char value);
byte get_exp_value(char pin);
#define EXP_P0    0
#define EXP_P1    1
#define EXP_P2    2
#define EXP_P3    3
#define EXP_P4    4
#define EXP_P5    5
#define EXP_P6    6
#define EXP_P7    7

// LEDS
#define LED_R           EXP_P1
#define SET_LED_R_HIGH  set_exp_value(LED_R, HIGH)
#define SET_LED_R_LOW   set_exp_value(LED_R, LOW)
#define LED_G           EXP_P0
#define SET_LED_G_HIGH  set_exp_value(LED_G, HIGH)
#define SET_LED_G_LOW   set_exp_value(LED_G, LOW)
char led_g_blink = 0;
unsigned long t_blink = 0;

// PULSADORES
#define BUTTON_1      EXP_P7
#define GET_B1        get_exp_value(BUTTON_1)
#define BUTTON_2      EXP_P6
#define GET_B2        get_exp_value(BUTTON_2)
char b1 = 0;
char b2 = 0;

// BLUETOOTH
#define BT            Serial
#define BAUDRATE      38400

// LECTURA DE BATERÍA
#define BAT           A0
unsigned int ADC_bat = 0;

#ifdef SEGUIMIENTO_CON_CAMARA
// CÁMARA
  #define CLK_CAM       2
  #define SI_CAM        7
  #define ANALOG_CAM    A1
  const int num_sensores = 8;
  int despreciar_primeras_lecturas = 5;
#else
// SENSORES DE LÍNEA
  #define SENSORES_LINEA_VELOCISTA // Morro para velocista (V1)

  #ifndef SENSORES_LINEA_VELOCISTA // Si no se ha definido el morro para velocista:
    #define SENSORES_LINEA_RASTREADOR // Morro para rastreador (V2)
  #endif

  #define LINEA_1       A2
  #define LINEA_2       A3
  #define LINEA_3       A4
  #define LINEA_SEL_1   12
  #define LINEA_SEL_2   13

  #ifdef SENSORES_LINEA_VELOCISTA // Número de sensores de línea del velocista
    const int num_sensores = 6;
  #else
    #ifdef SENSORES_LINEA_RASTREADOR // Número de sensores de línea del rastreador
      const int num_sensores = 8;
    #endif
  #endif

int despreciar_primeras_lecturas = 0;
#endif

#define IZQ 0
#define DER 1
int giro = IZQ;
unsigned int ADC_linea[num_sensores];
unsigned int negro[num_sensores];
unsigned int blanco[num_sensores];
unsigned int umbral[num_sensores];

// MOTORES
#define PWM_IZQ             6
#define PWM_DER             3
#define DIR_IZQ_1           EXP_P2
#define SET_DIR_IZQ_1_HIGH  set_exp_value(DIR_IZQ_1, HIGH)
#define SET_DIR_IZQ_1_LOW   set_exp_value(DIR_IZQ_1, LOW)
#define DIR_IZQ_2           EXP_P3
#define SET_DIR_IZQ_2_HIGH  set_exp_value(DIR_IZQ_2, HIGH)
#define SET_DIR_IZQ_2_LOW   set_exp_value(DIR_IZQ_2, LOW)
#define DIR_DER_1           EXP_P5
#define SET_DIR_DER_1_HIGH  set_exp_value(DIR_DER_1, HIGH)
#define SET_DIR_DER_1_LOW   set_exp_value(DIR_DER_1, LOW)
#define DIR_DER_2           EXP_P4
#define SET_DIR_DER_2_HIGH  set_exp_value(DIR_DER_2, HIGH)
#define SET_DIR_DER_2_LOW   set_exp_value(DIR_DER_2, LOW)

// TIMER
int periodo = 1; // milisegundos de periodo del timer
unsigned long t = 0;

// ESTADOS
#define INICIALIZADO          0
#define CALIBRANDO_SENSORES   1
#define PARADO                2
#define RASTREANDO            3
int estado = INICIALIZADO;

// VARIABLES
int velocidad = 80; // valor entre 0 y 255
int proporcional = 0;
long integral = 0;
long integral_max = 100;
int derivativo = 0;
int proporcional_anterior = 0;
int error = 0;
int error_max = 500;
float Kp = 0.3;
float Ki = 0;
float Kd = 10;


void setup() {
  pinMode(PWM_IZQ, OUTPUT);
  pinMode(PWM_DER, OUTPUT);

#ifdef SEGUIMIENTO_CON_CAMARA
  pinMode(CLK_CAM, OUTPUT);
  pinMode(SI_CAM, OUTPUT);

  // Start
  digitalWrite(SI_CAM, HIGH);
  digitalWrite(CLK_CAM, HIGH);
  digitalWrite(SI_CAM, LOW);
  digitalWrite(CLK_CAM, LOW);

  for(int i = 0; i < 128; i ++) {
    digitalWrite(CLK_CAM, HIGH);
    digitalWrite(CLK_CAM, LOW);
  }
#else
  pinMode(LINEA_SEL_1, OUTPUT);
  pinMode(LINEA_SEL_2, OUTPUT);
#endif

  BT.begin(BAUDRATE);
  EXP.begin();

  SET_LED_R_LOW;
  SET_LED_G_HIGH;
}

void loop() {
  if(millis() - t > periodo)
  {
    t = millis();
    leer_pulsadores();

    switch(estado) {
      case INICIALIZADO:
        if(b1 == HIGH)
        {
          for(int i=0; i<num_sensores; i++)
          {
            negro[i] = 0;
            blanco[i] = 1023;
          }
          estado = CALIBRANDO_SENSORES;
          SET_LED_G_LOW;
        }
        break;
        
      case CALIBRANDO_SENSORES:
        if(b2 == HIGH)
        {
          estado = PARADO;
          led_g_blink = 1;
        }
        break;

      case PARADO:
        if(b1 == HIGH)
        {
          estado = RASTREANDO;
          led_g_blink = 0;
        }
        break;
        
      case RASTREANDO:
        if(b2 == HIGH)
        {
          estado = PARADO;
          analogWrite(PWM_IZQ,0);
          analogWrite(PWM_DER,0);
          integral = 0;
          led_g_blink = 1;
        }
        break;
    }

    switch (estado) {
      case CALIBRANDO_SENSORES:
        static int var = 0;

        leer_sensores_linea(ADC_linea);
        var = 0;

        if(despreciar_primeras_lecturas > 0)
          despreciar_primeras_lecturas--;
        else
        {
          for(int i=0; i<num_sensores; i++)
          {
            if(ADC_linea[i] > negro[i])
            {
              negro[i] = ADC_linea[i];
              umbral[i] = (negro[i] + blanco[i])/2;
            }
            if(ADC_linea[i] < blanco[i])
            {
              blanco[i] = ADC_linea[i];
              umbral[i] = (negro[i] + blanco[i])/2;
            }
  
            if(negro[i]-blanco[i]> 100)
              var++;
          }
  
          if(var == num_sensores)
              SET_LED_G_HIGH;
        }

        break;
        
      case PARADO:
        if(t - t_blink < 250)
          SET_LED_G_LOW;
        else if(t - t_blink < 500)
          SET_LED_G_HIGH;
        else
          t_blink = t;
        break;

      case RASTREANDO:
        leer_sensores_linea(ADC_linea);
        proporcional = posicion_linea(ADC_linea);
        PID();
        control_motores();
        break;
    }

    leer_bateria();
    comandos();
  }
}

void set_exp_value(char pin, char value) {
  if(value == HIGH)
    expOutputRegister = expOutputRegister & (~(1<<pin));
  else // value == LOW
    expOutputRegister = expOutputRegister | (1<<pin);

  EXP.beginTransmission(expAddress);
  EXP.write(expOutputRegister);
  EXP.endTransmission();
}

byte get_exp_value(char pin) {
  byte value = 0;

  EXP.requestFrom(expAddress, 1);
  if(EXP.available())
    value = EXP.read();
  EXP.endTransmission();

  return (value & 1<<pin)>>pin;
}

void leer_pulsadores(void) {
  static unsigned int cont_b1 = 0;
  static unsigned int cont_b2 = 0;
  
  if(GET_B1 == LOW)
  {
    if(cont_b1 >= 20)
      b1 = HIGH;
    else
      cont_b1 += periodo;
  }
  else
  {
    b1 = LOW;
    cont_b1 = 0;
  }

  if(GET_B2 == LOW)
  {
    if(cont_b2 >= 20)
      b2 = HIGH;
    else
      cont_b2 += periodo;
  }
  else
  {
    b2 = LOW;
    cont_b2 = 0;
  }
}

void leer_bateria(void) {
  float tension_bateria = 0;
  
  ADC_bat = analogRead(BAT);
  tension_bateria = ADC_bat *5.0/1023 * (120+82)/120.0;

  if(tension_bateria < 7.4)
    SET_LED_R_HIGH;
  else if(tension_bateria > 7.6)
    SET_LED_R_LOW;
}

void leer_sensores_linea(unsigned int* value) {
#ifdef SEGUIMIENTO_CON_CAMARA
  // Starts pixel count
  digitalWrite(SI_CAM, HIGH);
  digitalWrite(CLK_CAM, HIGH);
  digitalWrite(SI_CAM, LOW);
  digitalWrite(CLK_CAM, LOW);
  
  // Pixel count and read
  int t = 0;
  for(int i = 0; i < 128; i++) {
    if(i>= (128-num_sensores)/2 && i < (128+num_sensores)/2)
    {
      value[t] = 1023 - analogRead(ANALOG_CAM);
      t++;
    }
    digitalWrite(CLK_CAM, HIGH);
    digitalWrite(CLK_CAM, LOW);
  }
#else
  #ifdef SENSORES_LINEA_VELOCISTA
    digitalWrite(LINEA_SEL_1, LOW);
    value[0] = analogRead(LINEA_1);
    value[2] = analogRead(LINEA_2);
    value[4] = analogRead(LINEA_3);
    digitalWrite(LINEA_SEL_1, HIGH);
    value[1] = analogRead(LINEA_1);
    value[3] = analogRead(LINEA_2);
    value[5] = analogRead(LINEA_3);
  #else
    #ifdef SENSORES_LINEA_RASTREADOR
      digitalWrite(LINEA_SEL_1, LOW);
      digitalWrite(LINEA_SEL_2, LOW);
      value[0] = analogRead(LINEA_1);
      value[4] = analogRead(LINEA_2);
      digitalWrite(LINEA_SEL_1, HIGH);
      digitalWrite(LINEA_SEL_2, LOW);
      value[1] = analogRead(LINEA_1);
      value[5] = analogRead(LINEA_2);
      digitalWrite(LINEA_SEL_1, LOW);
      digitalWrite(LINEA_SEL_2, HIGH);
      value[2] = analogRead(LINEA_1);
      value[6] = analogRead(LINEA_2);
      digitalWrite(LINEA_SEL_1, HIGH);
      digitalWrite(LINEA_SEL_2, HIGH);
      value[3] = analogRead(LINEA_1);
      value[7] = analogRead(LINEA_2);
    #endif
  #endif
#endif

  // Send data
//  for(int i = 0; i < num_sensores; i++) {
//    Serial.print(value[i]);
//    if(i == num_sensores-1)
//      Serial.println("\n");
//    else
//      Serial.print(" ");
//  }
}

int posicion_linea(unsigned int* value) {
  unsigned long sensores_media = 0;
  int sensores_suma = 0;
  int negros_detectados = 0;
  int pos = 0;
  unsigned int valor_linea[num_sensores];
  
  for(int i = 0; i < num_sensores; i++)       
  {
    if(value[i] < blanco[i])
      valor_linea[i] = blanco[i];
    else if(value[i] > negro[i])
      valor_linea[i] = negro[i];
    else
      valor_linea[i] = (value[i]-blanco[i]) * 1023.0 / (negro[i]-blanco[i]);

    if(value[i] > umbral[i])
      negros_detectados++;

    sensores_media += (unsigned long)valor_linea[i]*(i+1)*100;
    sensores_suma += valor_linea[i];
  }

  if(negros_detectados == 0)
  {
    if(giro == IZQ)
      pos = 1*100;
    else // giro == DER
      pos = (num_sensores)*100;
  }
  else
  {
    pos = sensores_media / sensores_suma;

    if(pos < ((num_sensores+1)*100/2))
      giro = IZQ;
    else if(pos > ((num_sensores+1)*100/2))
      giro = DER;
  }

  pos = pos - (num_sensores+1)*100/2;
  return pos;
}

/********************** ALGORITMO PID **********************/
void PID(void)
{
  integral = integral + proporcional;
  if(abs(integral) > integral_max)
  {
    if(integral > 0)
      integral = integral_max;
    else
      integral = -integral_max;
  }

  derivativo = proporcional - proporcional_anterior;
  proporcional_anterior = proporcional;

  error = (float)(proporcional * Kp + integral * Ki + derivativo * Kd);
}

void control_motores(void)
{
  int v_izq = 0, v_der = 0;
 
  if(error > error_max)
    error = error_max;
  else if(error < -error_max)
    error = -error_max;

  v_izq = velocidad + error;
  v_der = velocidad - error;

  if(v_izq > 255)
    v_izq = 255;
  else if(v_izq < -255)
    v_izq = -255;
  if(v_der > 255)
    v_der = 255;
  else if(v_der < -255)
    v_der = -255;

  if(v_izq >= 0)
  {
    SET_DIR_IZQ_1_HIGH;
    SET_DIR_IZQ_2_LOW;
  }
  else
  {
    SET_DIR_IZQ_1_LOW;
    SET_DIR_IZQ_2_HIGH;
  }

  if(v_der >= 0)
  {
    SET_DIR_DER_1_HIGH;
    SET_DIR_DER_2_LOW;
  }
  else
  {
    SET_DIR_DER_1_LOW;
    SET_DIR_DER_2_HIGH;
  }

  analogWrite(PWM_IZQ,abs(v_izq));
  analogWrite(PWM_DER,abs(v_der));
}

void comandos(void) {
  if (BT.available() > 0)
  {
    char inByte = 0;
    inByte = BT.read();

    switch(inByte)
    {
      case '1':
        if(Kp - 0.1 >= 0)
          Kp = Kp - 0.1;
        BT.print("Kp = ");
        BT.println(Kp);
        break;
        
      case '7':
        Kp = Kp + 0.1;
        BT.print("Kp = ");
        BT.println(Kp);
        break;
        
      case '2':
        if(Ki - 0.001 >= 0)
          Ki = Ki - 0.01;
        BT.print("Ki = ");
        BT.println(Ki);
        break;
        
      case '8':
        Ki = Ki + 0.01;
        BT.print("Ki = ");
        BT.println(Ki);
        break;
        
      case '3':
        if(Kd - 1 >= 0)
          Kd = Kd - 1;
        BT.print("Kd = ");
        BT.println(Kd);
        break;
        
      case '9':
        Kd = Kd + 1;
        BT.print("Kd = ");
        BT.println(Kd);
        break;
        
      case '-':
        if(velocidad - 5 >= 0)
          velocidad = velocidad - 5;
        BT.print("velocidad = ");
        BT.println(velocidad);
        break;

      case '+':
      if(velocidad + 5 <= 255)
        velocidad = velocidad + 5;
        BT.print("velocidad = ");
        BT.println(velocidad);
        break;

      case '0':
        estado = PARADO;
        analogWrite(PWM_IZQ,0);
        analogWrite(PWM_DER,0);
        integral = 0;
        SET_LED_G_HIGH;
        break;

      default:
        break;
    }
  }
}

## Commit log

2017-07-04 Kicad files added
    [Main_board.kicad_pcb, Main_board.sch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]
2017-07-04 Pin selection file added
    [PINSEL.xlsx]
2017-07-19 Motor driver position adjusted
    [Main_board.kicad_pcb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]
2017-07-28 BOMs and PDF schematic added
    [Main_board.csv, Main_board.kicad_pcb, Main_board.sch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]
2017-07-29 BOM added
    [BOM.xlsx]
2017-07-29 Some 3D designs added
    [Pantalla trasera.FCStd, Pantalla trasera.stl, Soporte micromotor (tornillos M2).stl]
2017-07-30 Screen modified
    [Pantalla trasera.FCStd, Pantalla trasera.stl]
2017-07-30 Sensor holder added
    [Main_board.kicad_pcb, Soporte de sensores de distancia.FCStd, Soporte simple de sensores de distancia.stl]
2017-07-30 BOM modified
    [BOM.xlsx]
2017-07-30 Sensors holder modified
    [Soporte de sensores de distancia.FCStd, Soporte simple de sensores de distancia.stl]
2017-07-30 Camera holder added
    [Soporte camara.FCStd, Soporte camara.stl]
2017-07-31 Batty connector modified in BOM
    [BOM.xlsx]
2017-07-31 Camera holder modified
    [Soporte camara.FCStd, Soporte camara.stl]
2017-07-31 Resistors modified
    [BOM.xlsx, Main_board.csv, Main_board.kicad_pcb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]
2017-08-01 DC-DC enable modified
    [Main_board.kicad_pcb, Main_board.sch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]
2017-08-01 Wheels link modified
    [BOM.xlsx, Main_board.kicad_pcb]
2017-08-02 Right angle male pin header link modified in BOM
    [BOM.xlsx]
2017-08-02 Link of lipo charger modified
    [BOM.xlsx]
2017-08-03 Wheels modified in BOM
    [BOM.xlsx]
2017-08-10 fw and hw folders added
    [BOM.xlsx, Main_board.csv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]
2017-08-13 Leds connections modified and I2C resistors added
    [Main_board.csv, Main_board.kicad_pcb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]
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2017-09-05 Gerbers actualized and motors connector changed
    [Main_board.kicad_pcb, Main_board.sch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]
2017-09-23 I2C resistor values changed
    [BOM.ods, BOM.xlsx, Main_board.csv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]
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2017-10-04 Bluetooth configuration added
    [Configuración Bluetooth HC-05.fzz]
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2017-11-05 Sheet for calculation of proporcional factor of PID added
    [Cálculo del proporcional del PID.ods]
2017-12-01 PCB silk modified
    [Main_board.kicad_pcb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]
2017-12-04 Pantalla trasera ampliada
    [Pantalla trasera.FCStd, Pantalla trasera.stl]
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2018-01-20 BOM modified
    BOM moved to hw folder
    [BOM.ods]
2018-01-20 Main_board version specified
    [Main_board.sch]
2018-01-20 Main_board V2 generated
    Diode added on Bluetooth Tx connection
    [Main_board.kicad_pcb, Main_board.ods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]
2018-01-20 Documentation modified for Main_board_V2
    [BOM.ods]
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2018-01-30 Modificadas rutas de librerias de Kicad
    [Main_board.sch]
2018-01-30 Cambiado valor del diodo D4
    [Main_board.kicad_pcb, Main_board.ods, Main_board.sch]
2018-01-30 Cambiado diodo D4 en tutorial y BOM
    [BOM.ods]
2018-02-15 Añadido soporte inclinable para camara Aliexpress.
    Se añade soporte con inclinación variable para la cámara de Aliexpress, Se requieren dos tornillos M2x8 adicionales.
    [Soporte_inclinable_camara_Aliexpress.stl]
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2018-07-12 Files updated with icons
    [Pantalla trasera.FCStd, Soporte camara APTech.FCStd, Soporte camara Aliexpress.FCStd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]
2018-07-12 PCBs silkscreen updated
    [Main_board.kicad_pcb, Main_board.sch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]
2018-08-07 PCBs adapted with Kicad libraries models
    [Main_board.kicad_pcb, Main_board.sch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]
2018-08-07 3D model for Arduino Nano socket added
    [Main_board.kicad_pcb]
2018-08-07 PCBs FreeCAD models created with Kicad StepUp
    [Main_board.FCStd, Sensors_board.FCStd, Sensors_board.step]
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2018-08-19 Silkscreen fixed
    [Main_board.kicad_pcb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]
2018-10-02 Añade control a través de la APP PIDfromBT
    Implementado control del PID del siguelineas a traves de la APP movil PIDfromBT para una experiencia de uso ALUCINANTE!!!
    Librería -> https://github.com/robotaleh/PIDfromBTlib
    APP -> https://github.com/robotaleh/PIDfromBT
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2018-11-25 3D model of basic assembly added
    [DIP-16_W7.62mm.step, Encoder disc.step, Lipo battery 2S.fcstd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]
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2018-12-13 Bug fixed
    [BOM.ods]
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2019-03-03 Some details changed
    [Main_board_V2.FCStd]
2019-03-03 Sensors_board_V2 Schematic, pdf and bom added
    [Sensors_board.kicad_pcb, Sensors_board.ods, Sensors_board.sch]
2019-03-04 PCB Sensors_board_V2 designed
    [Sensors_board.kicad_pcb]
2019-03-04 Ground plane modified
    [Sensors_board.kicad_pcb]
2019-03-04 Sensors_board_V2 3D files added
    [Sensors_board_V2.FCStd, Sensors_board_V2.step]
2019-03-04 Sensors_board_V2 gerbers added
    [Sensors_board-B.Cu.gbl, Sensors_board-B.Mask.gbs, Sensors_board-B.SilkS.gbo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]
2019-03-05 Included CD4052 socket
    [Sensors_board-B.Cu.gbl, Sensors_board-B.Mask.gbs, Sensors_board-B.SilkS.gbo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]
2019-03-05 Robot assembly with Sensors_board_V2 added
    [Sensors_board_V2.step]
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2019-03-06 PID proportional calculation for 8 sensors added
    [Cálculo del proporcional del PID.ods]
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2019-03-06 Modified BOM for added sensors_board_V2
    [BOM.ods]
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2019-03-06 Gerbers modified
    [Sensors_board_V2.gbl, Sensors_board_V2.gbo, Sensors_board_V2.gbs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]
2019-03-07 Changed BOM details
    [BOM.ods]
2019-04-01 Bug fixed in line sensors test
    [test.ino]
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2019-04-20 Front distance sensor height fixed to avoid multiplexer
    [Soporte de sensores de distancia.FCStd, Soporte sensores de distancia.stl]
2019-09-09 Modificados los gerbers de la PCB de sensores para rastreador
    [Sensors_board.kicad_pcb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]
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

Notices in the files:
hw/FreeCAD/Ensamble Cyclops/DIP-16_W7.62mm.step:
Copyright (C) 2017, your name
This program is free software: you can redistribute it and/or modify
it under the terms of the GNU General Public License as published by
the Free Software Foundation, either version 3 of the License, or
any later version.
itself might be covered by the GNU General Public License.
